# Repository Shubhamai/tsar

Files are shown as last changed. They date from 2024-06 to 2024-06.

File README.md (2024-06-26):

# Tsar

This repository contains Tsar flight computer that I have been developing for autonomous vehicles. The goal is to build a general-purpose & fully programmable flight computer that can be used for any autonomous model vehicles. The design is intended to be modular, cost-effective, and easy to manufacture.

The PCB is designed in KiCad and updated to version 8.0.3.

## Version History

### V3 [Latest Version]

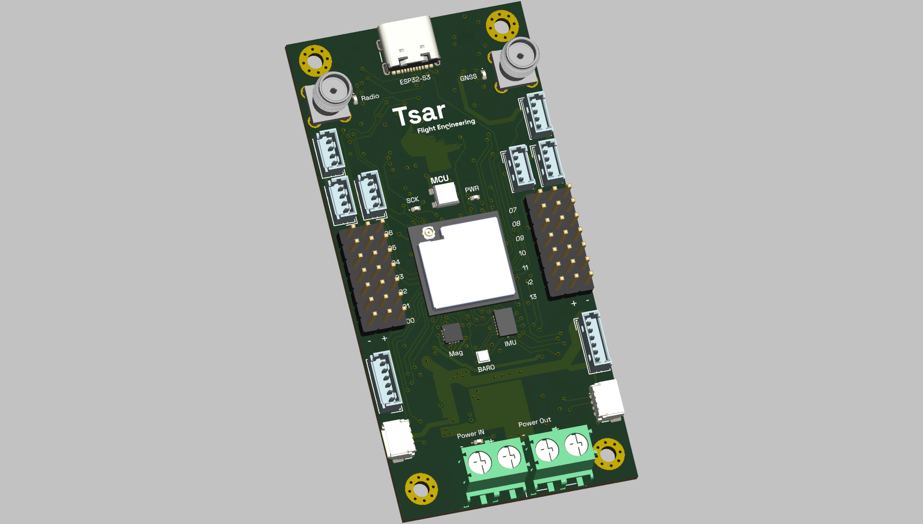
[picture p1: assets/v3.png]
V3


The design is very similar to V2 but with different IO style and no pyro channels. The secondary chip is STM32G0 for a lower number of components. The design is still in progress.

#### Key Features:
- Main Dual core ESP32-S3
- Secondary STM32G0 as an IO extender
- 2.4GHz SX1280 radio
- Ublox-M10S GNSS
- BMI088 IMU (up to ± 24 g, ± 2000°/s)
- BMP390 barometer (up to 10KM), MMC5983MA magnetometer for heading
- SD card and flash (ESP32-S3 inbuilt) for data logging & storage
- 14 PWM channels (combined 3A)
- ~20 auxiliary outputs with SPI, I2C, analog, digital pins, etc.
- 6-16V power input, (reverse+over+under)-voltage, over-current protection
- Dimensions: 40mm width, 82mm height

### V2 [April 2024]

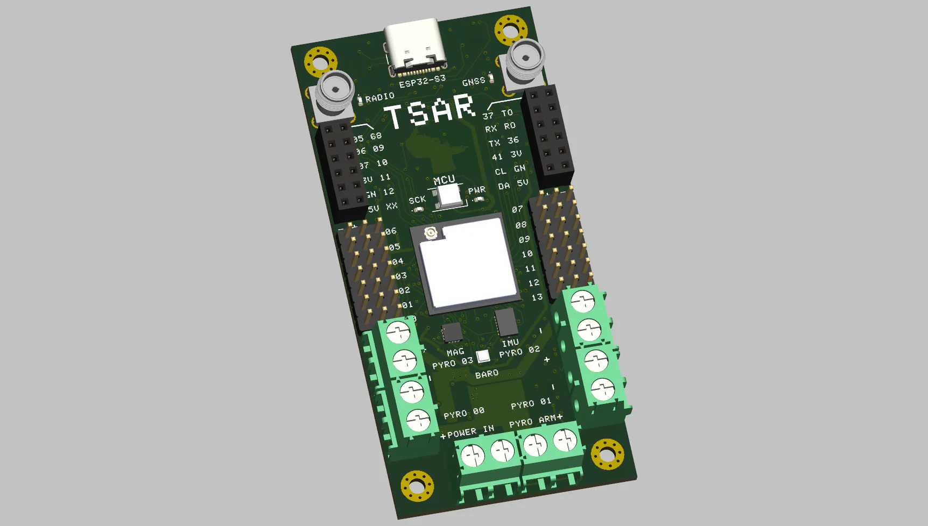
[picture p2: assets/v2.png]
V2


With learnings from V1, V2 was designed to be more cost-effective, less complex, and easier to manufacture. The BOM cost was around $60-80, and the board had 4 layers. With a trace width and minimum clearance of 0.2mm, QFN chips, and 0603 components, it was easier to manufacture and assemble. The board was manufactured and partially tested but not yet used in flight.

#### Key Features:
- Main Dual core ESP32-S3
- Secondary RP2040 as an IO extender
- 2.4GHz SX1280 radio
- Ublox-M10S GNSS
- BMI088 IMU (up to ± 24 g, ± 2000°/s)
- BMP390 barometer (up to 10KM), MMC5983MA magnetometer for heading
- 4 pyro channels (up to 16V, 4A) with continuity
- SD card and flash (ESP32-S3 inbuilt) for data logging & storage
- 14 PWM channels (combined 3A)
- 17 auxiliary outputs with SPI, I2C, analog, digital pins, etc.
- 6-16V power input, (reverse+over+under)-voltage, over-current protection
- Dimensions: 40mm width, 82mm height

### V1 [March 2024]

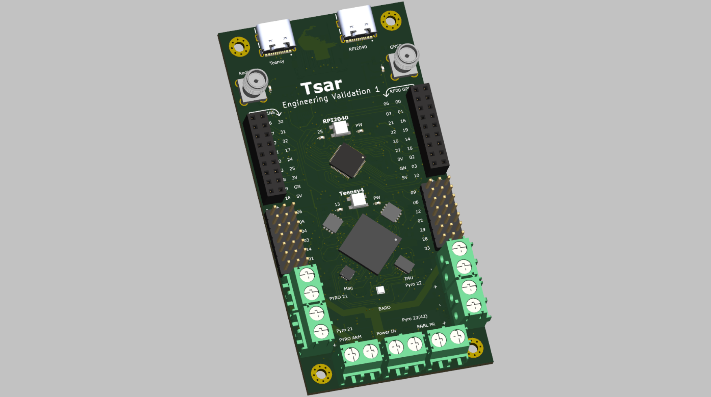
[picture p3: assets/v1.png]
V1


The first attempt at designing a flight computer. The design was powerful, using Teensy, but highly complex and less cost-effective. The BOM cost was around $120-150, and the board had 4 layers. With a trace width and minimum clearance of 0.127mm, BGA chips, and 0402 components, it was challenging to manufacture and assemble. This version was never manufactured or tested.

#### Key Features:
- Main Chip: NXP IMXRT106DVJ6B (Teensy 4.1)
- RP2040 as an IO extender
- 2.4GHz SX1280 radio
- Ublox-M10S GNSS
- BMI088 IMU (up to ± 24 g, ± 2000°/s)
- BMP390 barometer (up to 10KM), MMC5983MA magnetometer for heading
- 4 pyro channels (up to 16V, 4A) with continuity
- SD card and flash for data logging & storage
- 14 PWM channels (combined 3A)
- 30 auxiliary outputs with SPI, I2C, analog, digital pins, etc.
- 6-16V power input, (reverse+over+under)-voltage, over-current protection
- Dimensions: 50mm width, 100mm height

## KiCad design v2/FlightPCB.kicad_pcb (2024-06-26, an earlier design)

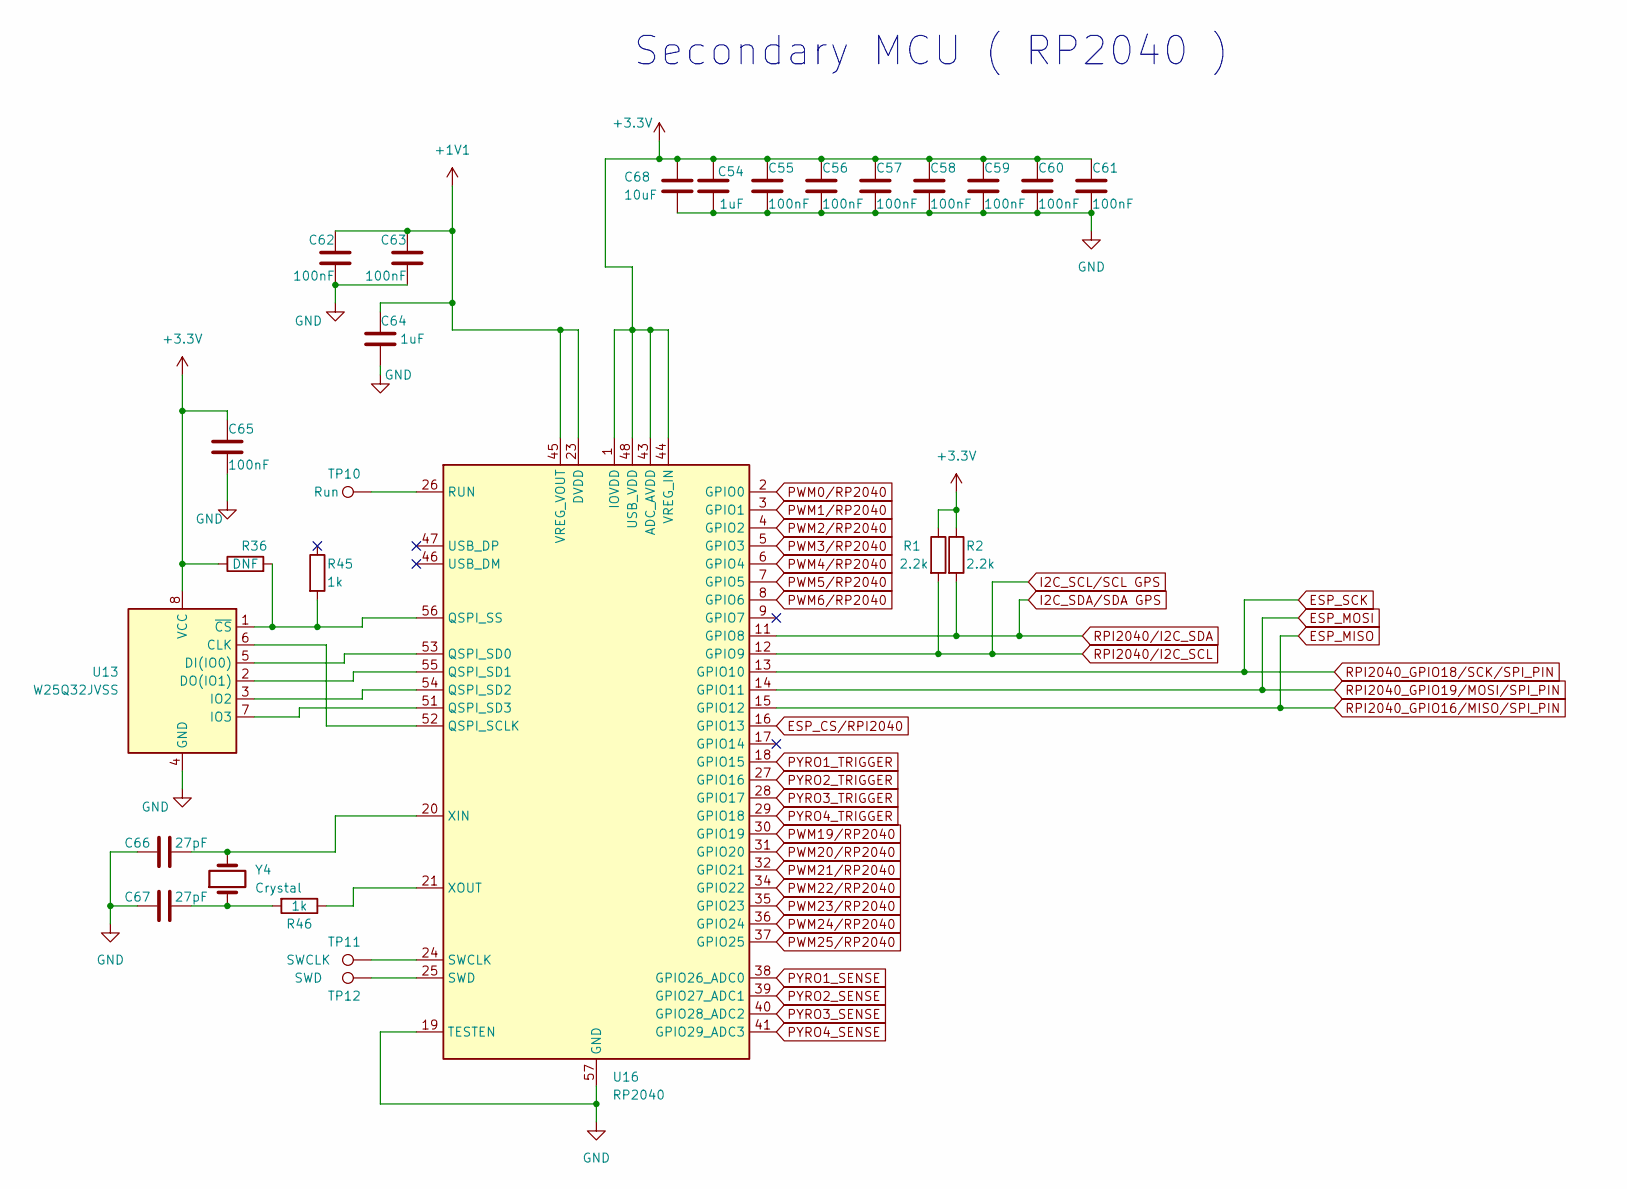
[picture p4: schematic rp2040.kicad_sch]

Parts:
C54, C64: 1uF; C_0603_1608Metric
C55, C56, C57, C58, C59, C60, C61, C62, C63, C65: 100nF; C_0603_1608Metric
C66, C67: 27pF; C_0603_1608Metric
C68: 10uF; C_0603_1608Metric
R1, R2: 2.2k; R_0603_1608Metric
R36: DNF; R_0402_1005Metric
R45, R46: 1k; R_0402_1005Metric
TP10: Run; TestPoint_Pad_D1.0mm
TP11: SWCLK; TestPoint_Pad_D2.0mm
TP12: SWD; TestPoint_Pad_D2.0mm
U13: W25Q32JVSS; SOIC-8_5.23x5.23mm_P1.27mm
U16: RP2040; QFN-56-1EP_7x7mm_P0.4mm_EP4x4mm
Y4: Crystal; Crystal_SMD_Abracon_ABM8G-4Pin_3.2x2.5mm

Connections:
+1V1: C62.1, C63.1, C64.1, U16.23 (DVDD), U16.45 (VREG_VOUT), U16.50 (DVDD)
+3.3V: C54.1, C55.1, C56.1, C57.1, C58.1, C59.1, C60.1, C61.1, C65.1, C68.1, R1.1, R2.1, R36.1, U13.8 (VCC), U16.1 (IOVDD), U16.10 (IOVDD), U16.22 (IOVDD), U16.33 (IOVDD), U16.42 (IOVDD), U16.43 (ADC_AVDD), U16.44 (VREG_IN), U16.48 (USB_VDD), U16.49 (IOVDD); also elsewhere on the board
BARO_MISO: U16.15 (GPIO12); also elsewhere on the board
BARO_MOSI: U16.14 (GPIO11); also elsewhere on the board
BARO_SCK: U16.13 (GPIO10); also elsewhere on the board
ESP_CS/RPI2040: U16.16 (GPIO13); also elsewhere on the board
ESP_SCL: R1.2, U16.12 (GPIO9); also elsewhere on the board
ESP_SDA: R2.2, U16.11 (GPIO8); also elsewhere on the board
GND: C54.2, C55.2, C56.2, C57.2, C58.2, C59.2, C60.2, C61.2, C62.2, C63.2, C64.2, C65.2, C66.1, C67.2, C68.2, U13.4 (GND), U16.19 (TESTEN), U16.57 (GND); also elsewhere on the board
unnamed: C67.1, R46.2, Y4.1
unnamed: U13.6 (CLK), U16.52 (QSPI_SCLK)
unnamed: U13.5 (DI(IO0)), U16.53 (QSPI_SD0)
unnamed: U13.2 (DO(IO1)), U16.55 (QSPI_SD1)
unnamed: U13.3 (IO2), U16.54 (QSPI_SD2)
unnamed: U13.7 (IO3), U16.51 (QSPI_SD3)
unnamed: R36.2, R45.2, U13.1 (~CS), U16.56 (QSPI_SS)
unnamed: TP10.1, U16.26 (RUN)
unnamed: TP11.1, U16.24 (SWCLK)
unnamed: TP12.1, U16.25 (SWD)
unnamed: C66.2, U16.20 (XIN), Y4.2
unnamed: R46.1, U16.21 (XOUT)
PWM0/RP2040: U16.2 (GPIO0); also elsewhere on the board
PWM1/RP2040: U16.3 (GPIO1); also elsewhere on the board
PWM2/RP2040: U16.4 (GPIO2); also elsewhere on the board
PWM3/RP2040: U16.5 (GPIO3); also elsewhere on the board
PWM4/RP2040: U16.6 (GPIO4); also elsewhere on the board
PWM5/RP2040: U16.7 (GPIO5); also elsewhere on the board
PWM6/RP2040: U16.8 (GPIO6); also elsewhere on the board
PWM19/RP2040: U16.30 (GPIO19); also elsewhere on the board
PWM20/RP2040: U16.31 (GPIO20); also elsewhere on the board
PWM21/RP2040: U16.32 (GPIO21); also elsewhere on the board
PWM22/RP2040: U16.34 (GPIO22); also elsewhere on the board
PWM23/RP2040: U16.35 (GPIO23); also elsewhere on the board
PWM24/RP2040: U16.36 (GPIO24); also elsewhere on the board
PWM25/RP2040: U16.37 (GPIO25); also elsewhere on the board
PYRO1_SENSE: U16.38 (GPIO26_ADC0); also elsewhere on the board
PYRO1_TRIGGER: U16.18 (GPIO15); also elsewhere on the board
PYRO2_SENSE: U16.39 (GPIO27_ADC1); also elsewhere on the board
PYRO2_TRIGGER: U16.27 (GPIO16); also elsewhere on the board
PYRO3_SENSE: U16.40 (GPIO28_ADC2); also elsewhere on the board
PYRO3_TRIGGER: U16.28 (GPIO17); also elsewhere on the board
PYRO4_SENSE: U16.41 (GPIO29_ADC3); also elsewhere on the board
PYRO4_TRIGGER: U16.29 (GPIO18); also elsewhere on the board

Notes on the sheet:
Secondary MCU ( RP2040 )

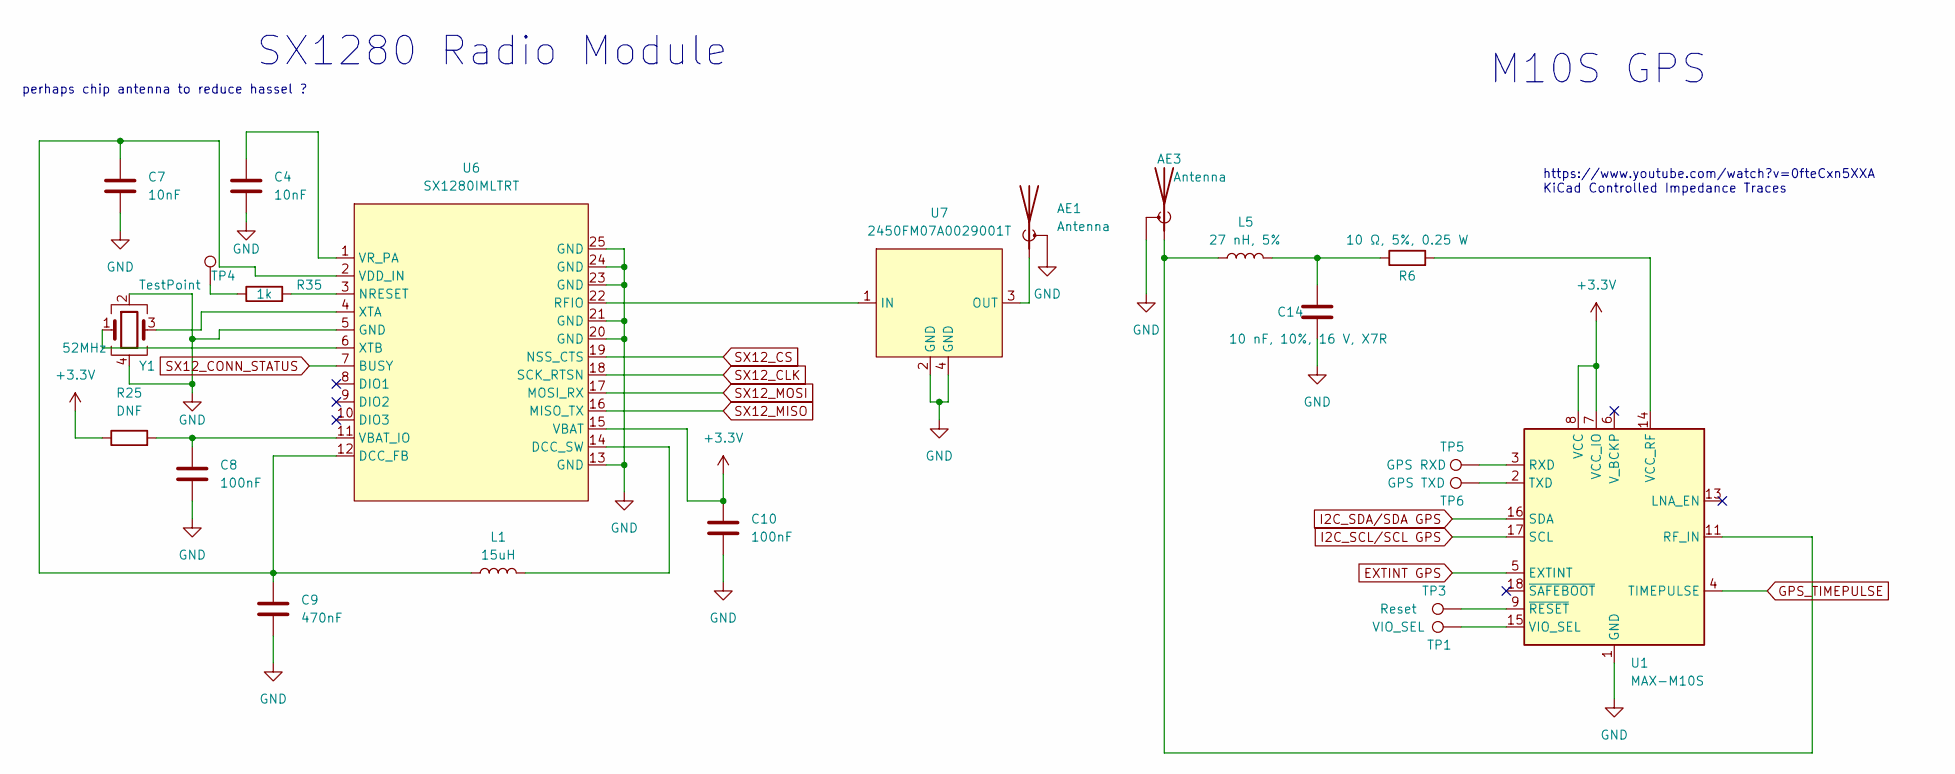
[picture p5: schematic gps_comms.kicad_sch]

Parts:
AE1, AE3: Antenna; SMA_Amphenol_901-144_Vertical
C4, C7: 10nF; C_0603_1608Metric
C8, C10: 100nF; C_0603_1608Metric
C9: 470nF; C_0402_1005Metric
C14: 10 nF, 10%, 16 V, X7R; C_0603_1608Metric
L1: 15uH; L_0805_2012Metric
L5: 27 nH, 5%; L_0402_1005Metric
R6: 10 Ω, 5%, 0.25 W; R_0402_1005Metric
R25: DNF; R_0402_1005Metric
R35: 1k; R_0402_1005Metric
TP1: VIO_SEL; TestPoint_Pad_D1.0mm
TP3: Reset; TestPoint_Pad_D1.0mm
TP4: TestPoint; TestPoint_Pad_D1.0mm
TP5: GPS RXD; TestPoint_Pad_D1.0mm
TP6: GPS TXD; TestPoint_Pad_D1.0mm
U1: MAX-M10S; ublox_MAX
U6: SX1280IMLTRT; QFN-24-1EP_4x4mm_P0.5mm_EP2.7x2.7mm
U7: 2450FM07A0029001T
Y1: 52MHz; Crystal_SMD_2016-4Pin_2.0x1.6mm

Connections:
+3.3V: C10.1, R25.1, U1.7 (VCC_IO), U1.8 (VCC), U6.15 (VBAT); also elsewhere on the board
BARO_MISO: U6.16 (MISO_TX); also elsewhere on the board
BARO_MOSI: U6.17 (MOSI_RX); also elsewhere on the board
BARO_SCK: U6.18 (SCK_RTSN); also elsewhere on the board
ESP_SCL: U1.17 (SCL); also elsewhere on the board
ESP_SDA: U1.16 (SDA); also elsewhere on the board
EXTINT GPS: U1.5 (EXTINT); also elsewhere on the board
GND: AE1.2 (Shield), AE3.2 (Shield), C4.2, C7.2, C8.2, C9.2, C10.2, C14.1, U1.1 (GND), U1.10 (GND), U1.12 (GND), U6.5 (GND), U6.13 (GND), U6.20 (GND), U6.21 (GND), U6.23 (GND), U6.24 (GND), U6.25 (GND), U7.2 (GND), U7.4 (GND), Y1.2, Y1.4; also elsewhere on the board
GPS_TIMEPULSE: U1.4 (TIMEPULSE); also elsewhere on the board
unnamed: AE1.1 (A), U7.3 (OUT)
unnamed: AE3.1 (A), L5.1, U1.11 (RF_IN)
unnamed: C14.2, L5.2, R6.1
unnamed: R35.1, TP4.1
unnamed: TP5.1, U1.3 (RXD)
unnamed: TP6.1, U1.2 (TXD)
unnamed: R6.2, U1.14 (VCC_RF)
unnamed: TP1.1, U1.15 (VIO_SEL)
unnamed: TP3.1, U1.9 (~RESET)
unnamed: C7.1, C9.1, L1.1, U6.2 (VDD_IN), U6.12 (DCC_FB)
unnamed: L1.2, U6.14 (DCC_SW)
unnamed: R35.2, U6.3 (NRESET)
unnamed: U6.22 (RFIO), U7.1 (IN)
unnamed: C8.1, R25.2, U6.11 (VBAT_IO)
unnamed: C4.1, U6.1 (VR_PA)
unnamed: U6.4 (XTA), Y1.3
unnamed: U6.6 (XTB), Y1.1
SX12_CONN_STATUS: U6.7 (BUSY); also elsewhere on the board
SX12_CS: U6.19 (NSS_CTS); also elsewhere on the board

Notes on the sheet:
perhaps chip antenna to reduce hassel ?
https://www.youtube.com/watch?v=0fteCxn5XXA KiCad Controlled Impedance Traces
M10S GPS
SX1280 Radio Module

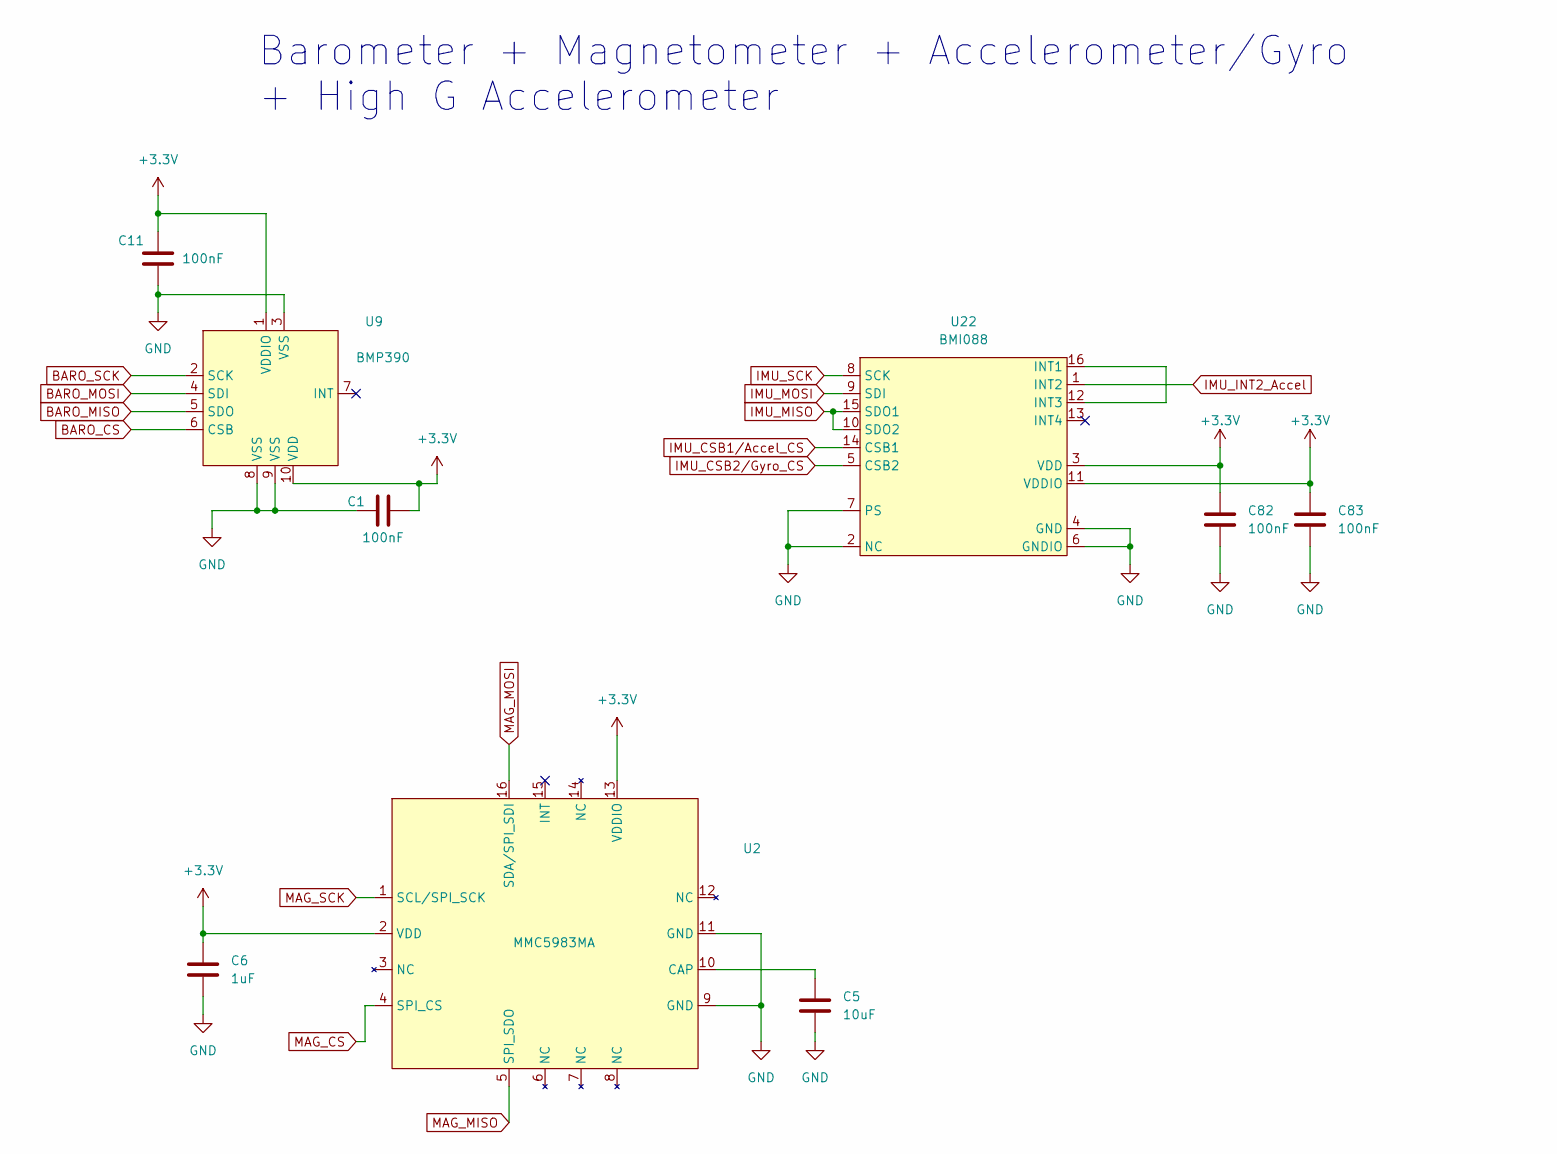
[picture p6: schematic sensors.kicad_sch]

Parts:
C1, C11, C82, C83: 100nF; C_0603_1608Metric
C5: 10uF; C_0603_1608Metric
C6: 1uF; C_0603_1608Metric
U2: MMC5983MA
U9: BMP390
U22: BMI088

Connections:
+3.3V: C1.2, C6.1, C11.2, C82.1, C83.1, U2.2 (VDD), U2.13 (VDDIO), U9.1 (VDDIO), U9.10 (VDD), U22.3 (VDD), U22.11 (VDDIO); also elsewhere on the board
BARO_CS: U9.6 (CSB); also elsewhere on the board
BARO_MISO: U2.5 (SPI_SDO), U9.5 (SDO), U22.10 (SDO2), U22.15 (SDO1); also elsewhere on the board
BARO_MOSI: U2.16 (SDA/SPI_SDI), U9.4 (SDI), U22.9 (SDI); also elsewhere on the board
BARO_SCK: U2.1 (SCL/SPI_SCK), U9.2 (SCK), U22.8 (SCK); also elsewhere on the board
GND: C1.1, C5.2, C6.2, C11.1, C82.2, C83.2, U2.9 (GND), U2.11 (GND), U9.3 (VSS), U9.8 (VSS), U9.9 (VSS), U22.2 (NC), U22.4 (GND), U22.6 (GNDIO), U22.7 (PS); also elsewhere on the board
IMU_CSB1/Accel_CS: U22.14 (CSB1); also elsewhere on the board
IMU_CSB2/Gyro_CS: U22.5 (CSB2); also elsewhere on the board
IMU_INT2_Accel: U22.1 (INT2); also elsewhere on the board
MAG_CS: U2.4 (SPI_CS); also elsewhere on the board
unnamed: C5.1, U2.10 (CAP)
unnamed: U22.12 (INT3), U22.16 (INT1)

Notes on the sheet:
Barometer + Magnetometer + Accelerometer/Gyro + High G Accelerometer

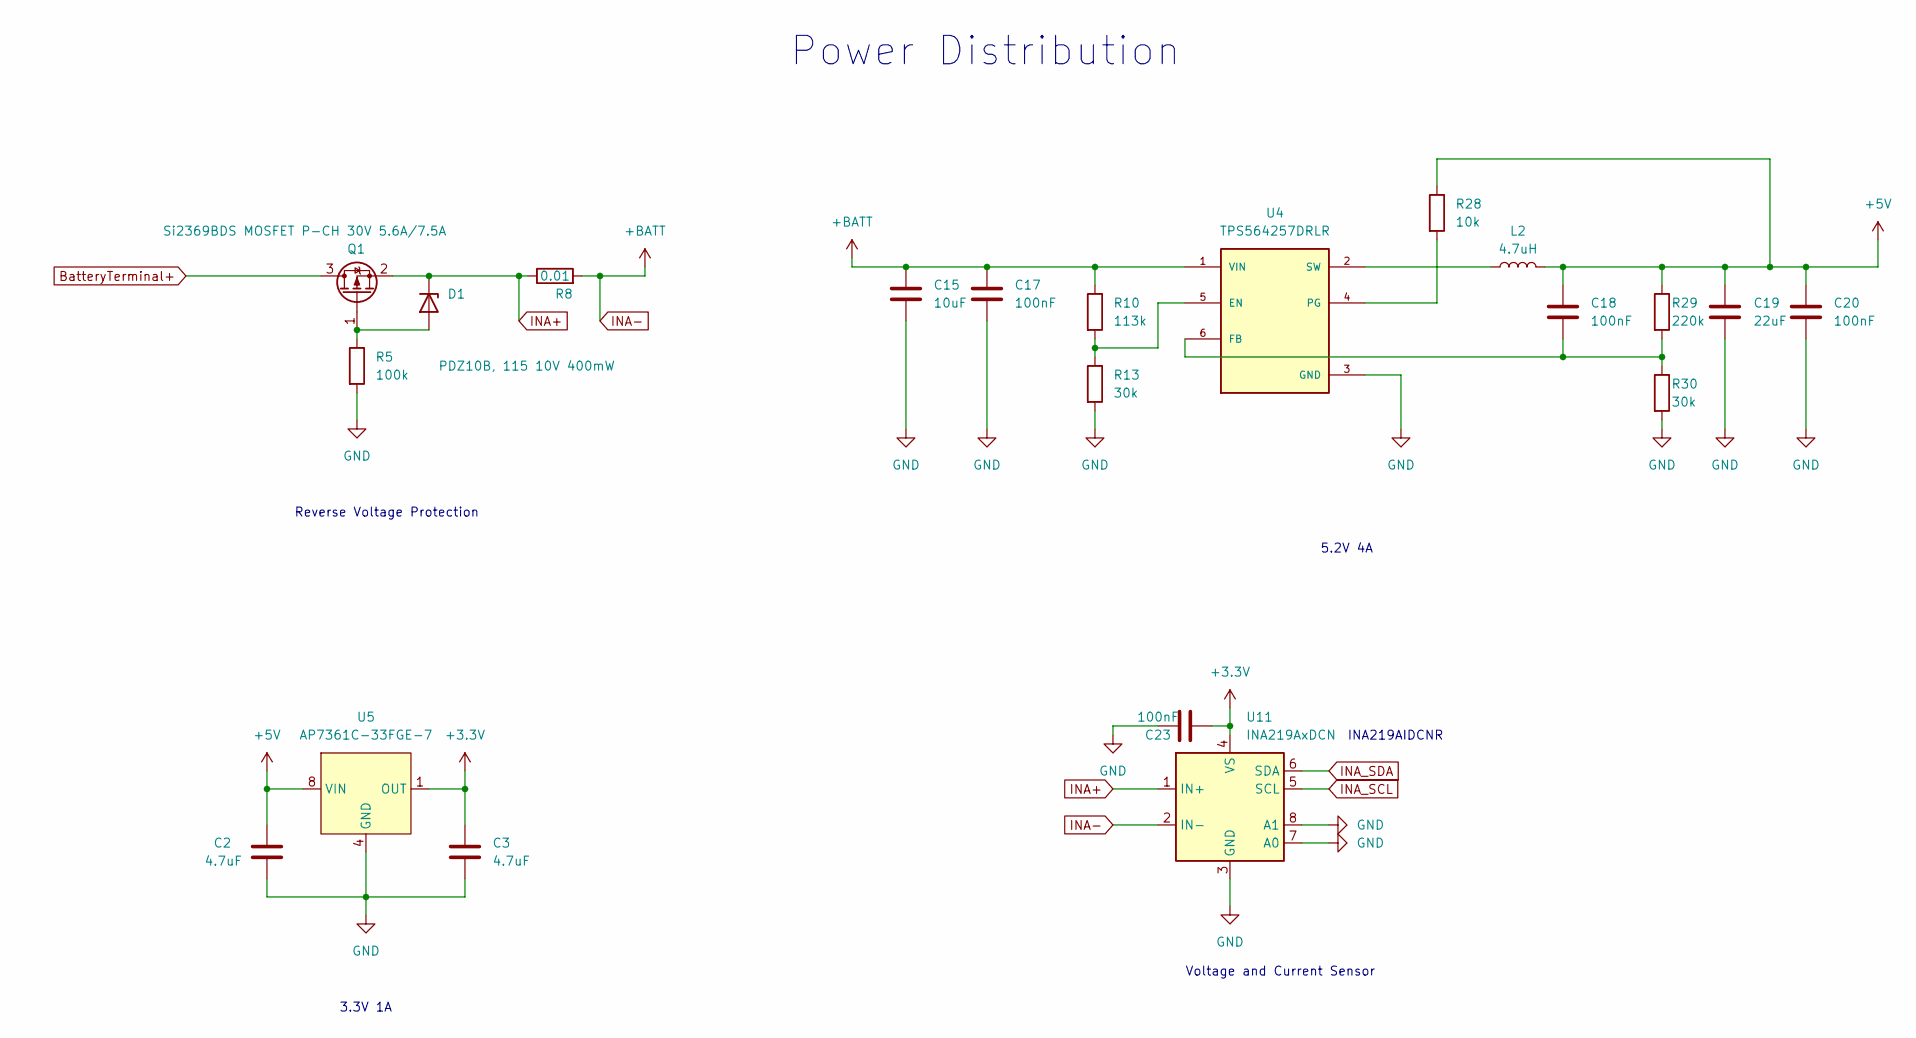
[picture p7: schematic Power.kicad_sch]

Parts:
C2, C3: 4.7uF; C_0603_1608Metric
C15: 10uF; C_0603_1608Metric
C17, C18, C20, C23: 100nF; C_0603_1608Metric
C19: 22uF; C_0805_2012Metric
D1: PDZ10B, 115 10V 400mW; D_0805_2012Metric
L2: 4.7uH; L_Cenker_CKCS8040
Q1: Si2369BDS MOSFET P-CH 30V 5.6A/7.5A; SOT-23
R5: 100k; R_0805_2012Metric
R8: 0.01; R_2512_6332Metric
R10: 113k; R_0603_1608Metric
R13, R30: 30k; R_0603_1608Metric
R28: 10k; R_0603_1608Metric
R29: 220k; R_0603_1608Metric
U4: TPS564257DRLR; SOT50P160X60-6N; PARTREV A
U5: AP7361C-33FGE-7; MLF-8-1EP_3x3mm_P0.65mm_EP1.55x2.3mm
U11: INA219AxDCN; SOT-23-8

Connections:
+3.3V: C3.1, C23.2, U5.1 (OUT), U11.4 (VS); also elsewhere on the board
BatteryTerminal+: Q1.3 (D); also elsewhere on the board
ESP_SCL: U11.5 (SCL); also elsewhere on the board
ESP_SDA: U11.6 (SDA); also elsewhere on the board
GND: C2.2, C3.2, C15.2, C17.2, C19.2, C20.2, C23.1, R5.2, R13.2, R30.2, U4.3 (GND), U5.4 (GND), U11.3 (GND), U11.7 (A0), U11.8 (A1); also elsewhere on the board
INA+: D1.1 (K), Q1.2 (S), R8.1, U11.1 (IN+)
INA-: C15.1, C17.1, R8.2, R10.1, U4.1 (VIN), U11.2 (IN-); also elsewhere on the board
unnamed: D1.2 (A), Q1.1 (G), R5.1
unnamed: R10.2, R13.1, U4.5 (EN)
unnamed: C18.2, R29.2, R30.1, U4.6 (FB)
unnamed: R28.2, U4.4 (PG)
unnamed: L2.1, U4.2 (SW)

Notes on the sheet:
INA219AIDCNR
Voltage and Current Sensor
3.3V 1A
Reverse Voltage Protection
5.2V 4A
Power Distribution

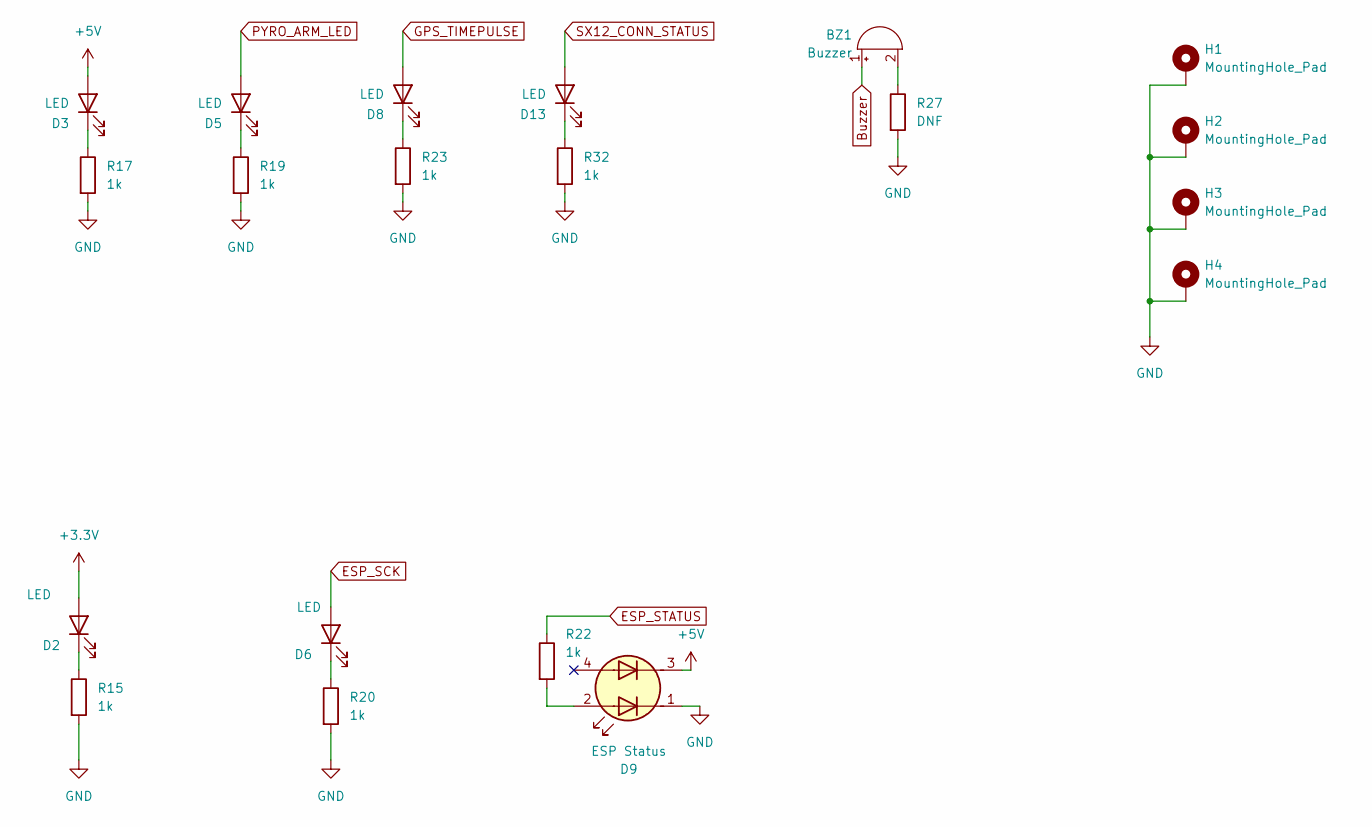
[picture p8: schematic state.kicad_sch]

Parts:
BZ1: Buzzer; Buzzer_CUI_CPT-9019S-SMT
D2, D3, D5, D6, D8, D13: LED; LED_0402_1005Metric
D9: ESP Status; IN-PI22TAT5R5G5B
H1, H2, H3, H4: MountingHole_Pad; MountingHole_2.7mm_M2.5_Pad_Via
R15, R17, R19, R20, R22, R23, R32: 1k; R_0402_1005Metric
R27: DNF; R_0402_1005Metric

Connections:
+3.3V: D2.2 (A); also elsewhere on the board
BARO_SCK: D6.2 (A); also elsewhere on the board
Buzzer: BZ1.1 (+); also elsewhere on the board
ESP_STATUS: R22.1; also elsewhere on the board
GND: D9.1 (A1), H1.1, H2.1, H3.1, H4.1, R15.2, R17.2, R19.2, R20.2, R23.2, R27.2, R32.2; also elsewhere on the board
GPS_TIMEPULSE: D8.2 (A); also elsewhere on the board
unnamed: BZ1.2 (-), R27.1
unnamed: D2.1 (K), R15.1
unnamed: D3.1 (K), R17.1
unnamed: D5.1 (K), R19.1
unnamed: D6.1 (K), R20.1
unnamed: D8.1 (K), R23.1
unnamed: D9.2 (K1), R22.2
unnamed: D13.1 (K), R32.1
PYRO_ARM_LED: D5.2 (A); also elsewhere on the board
SX12_CONN_STATUS: D13.2 (A); also elsewhere on the board

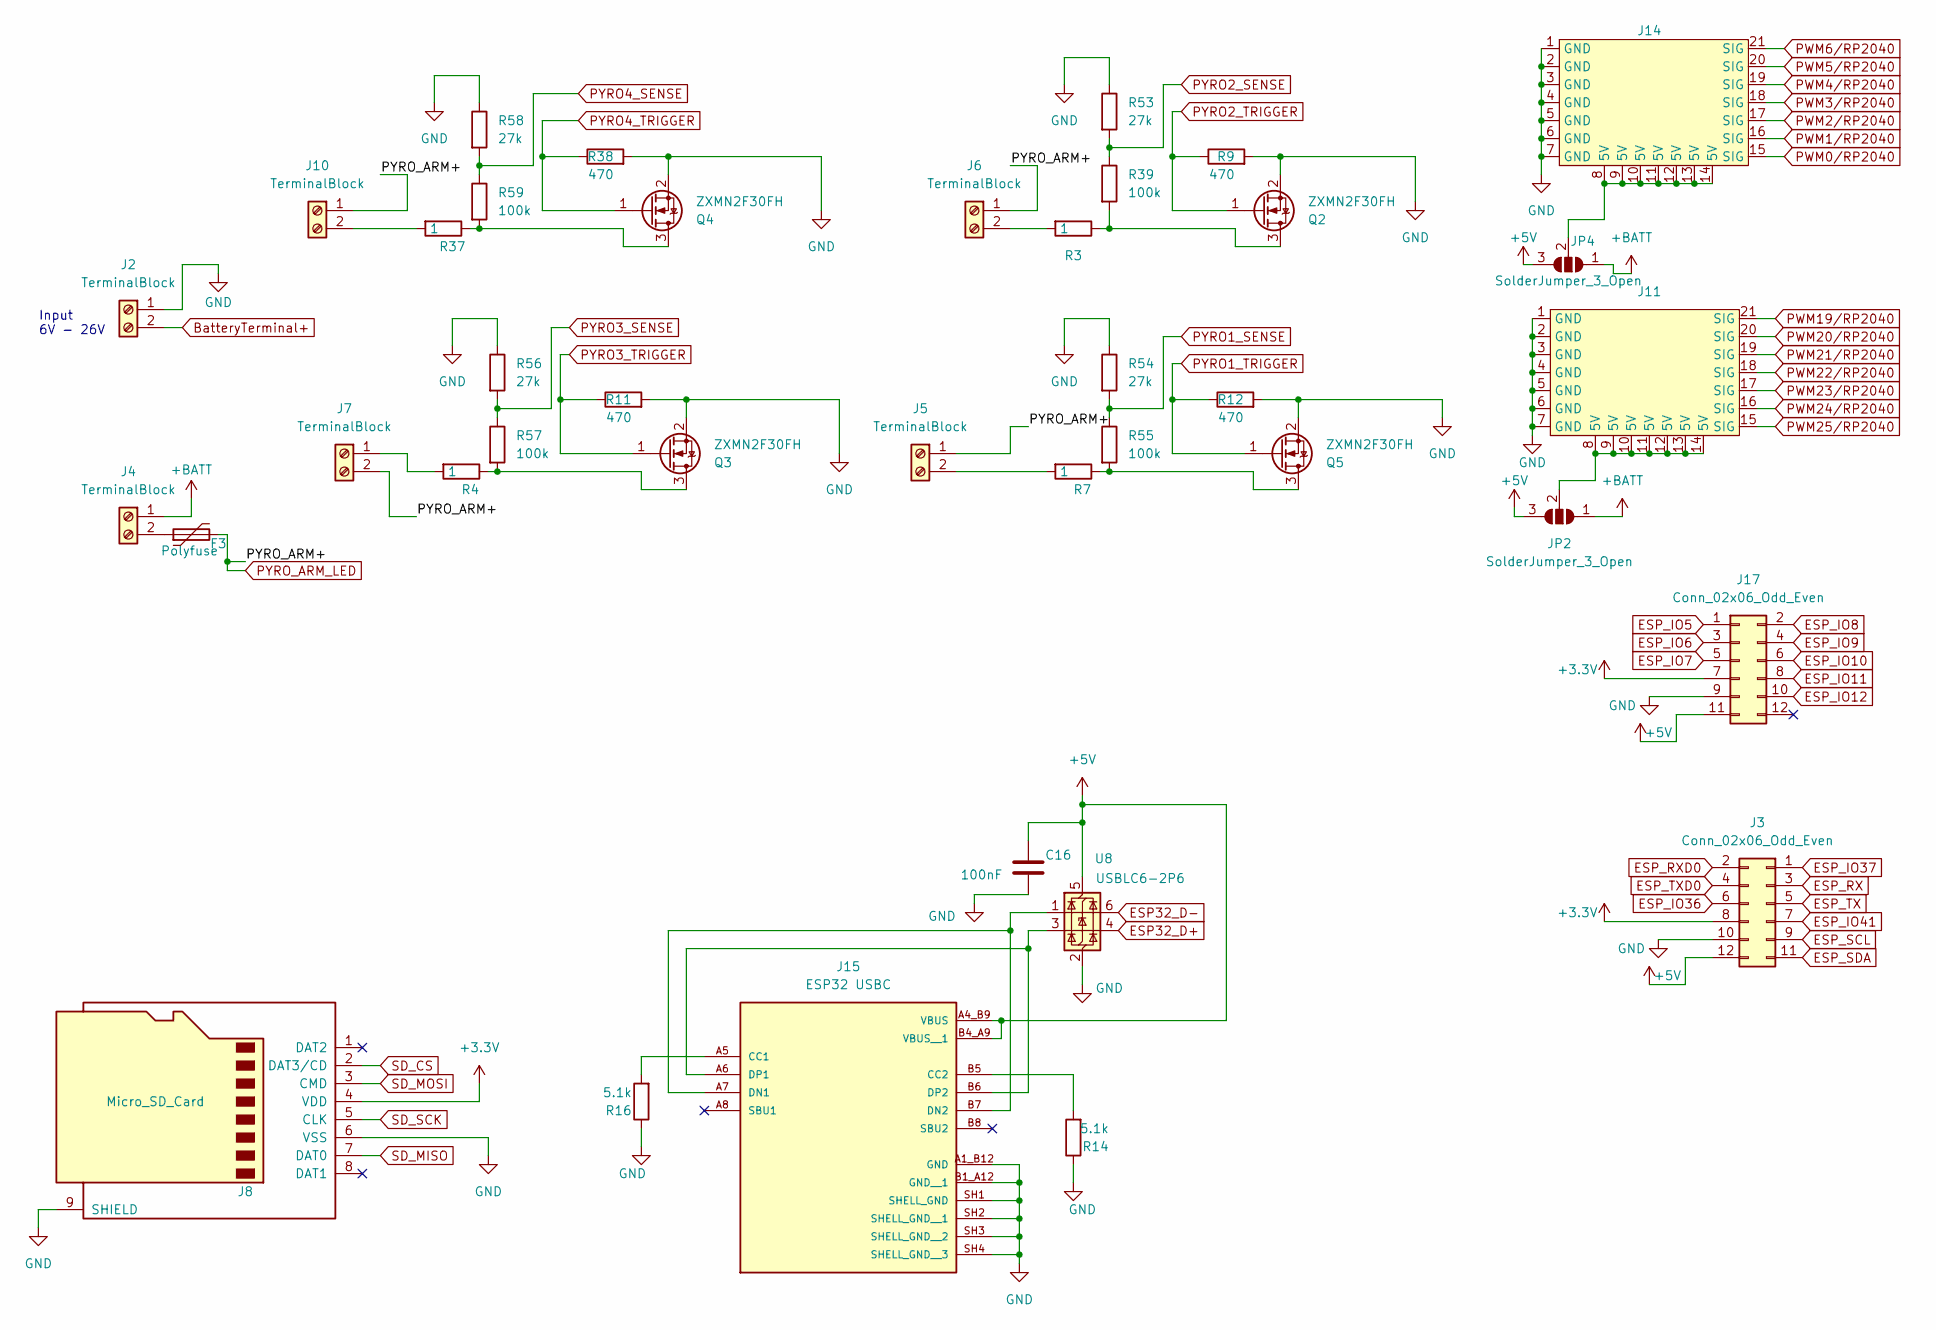
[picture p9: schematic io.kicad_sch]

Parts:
C16: 100nF; C_0603_1608Metric
F3: Polyfuse; Fuse_1812_4532Metric
J2, J4, J5, J6, J7, J10: TerminalBlock; TerminalBlock_Phoenix_PT-1,5-2-5.0-H_1x02_P5.00mm_Horizontal
J3, J17: Conn_02x06_Odd_Even; PinSocket_2x06_P2.54mm_Vertical
J8: Micro_SD_Card; microSD_HC_Molex_47219-2001
J11: PinHeader_3x05_P2.54mm_Vertical_Left
J14: PinHeader_3x05_P2.54mm_Vertical_Right
J15: ESP32 USBC; GCT_USB4105-GF-A; PARTREV B3
JP2, JP4: SolderJumper_3_Open; SolderJumper-3_P2.0mm_Open_TrianglePad1.0x1.5mm
Q2, Q3, Q4, Q5: ZXMN2F30FH; SOT-23
R3, R4, R7, R37: 1; R_0603_1608Metric
R9, R11, R12, R38: 470; R_0603_1608Metric
R14, R16: 5.1k; R_0603_1608Metric
R39, R55, R57, R59: 100k; R_0805_2012Metric
R53, R54, R56, R58: 27k; R_0603_1608Metric
U8: USBLC6-2P6; SOT-666

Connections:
+3.3V: J3.8, J8.4 (VDD), J17.7; also elsewhere on the board
BARO_MISO: J8.7 (DAT0); also elsewhere on the board
BARO_MOSI: J8.3 (CMD); also elsewhere on the board
BARO_SCK: J8.5 (CLK); also elsewhere on the board
BatteryTerminal+: J2.2; also elsewhere on the board
ESP32_D+: U8.4 (I/O2); also elsewhere on the board
ESP32_D-: U8.6 (I/O1); also elsewhere on the board
ESP_IO5: J17.1; also elsewhere on the board
ESP_IO6: J17.3; also elsewhere on the board
ESP_IO7: J17.5; also elsewhere on the board
ESP_IO8: J17.2; also elsewhere on the board
ESP_IO9: J17.4; also elsewhere on the board
ESP_IO10: J17.6; also elsewhere on the board
ESP_IO11: J17.8; also elsewhere on the board
ESP_IO12: J17.10; also elsewhere on the board
ESP_IO36: J3.6; also elsewhere on the board
ESP_IO37: J3.1; also elsewhere on the board
ESP_IO41: J3.7; also elsewhere on the board
ESP_RX: J3.3; also elsewhere on the board
ESP_RXD0: J3.2; also elsewhere on the board
ESP_SCL: J3.9; also elsewhere on the board
ESP_SDA: J3.11; also elsewhere on the board
ESP_TX: J3.5; also elsewhere on the board
ESP_TXD0: J3.4; also elsewhere on the board
GND: C16.2, J2.1, J3.10, J8.6 (VSS), J8.9 (SHIELD), J11.1 (GND), J11.2 (GND), J11.3 (GND), J11.4 (GND), J11.5 (GND), J11.6 (GND), J11.7 (GND), J14.1 (GND), J14.2 (GND), J14.3 (GND), J14.4 (GND), J14.5 (GND), J14.6 (GND), J14.7 (GND), J15.A1_B12 (GND), J15.B1_A12 (GND__1), J15.SH1 (SHELL_GND), J15.SH2 (SHELL_GND__1), J15.SH3 (SHELL_GND__2), J15.SH4 (SHELL_GND__3), J17.9, Q2.2 (S), Q3.2 (S), Q4.2 (S), Q5.2 (S), R9.2, R11.2, R12.2, R14.1, R16.1, R38.2, R53.1, R54.1, R56.1, R58.1, U8.2 (GND); also elsewhere on the board
INA-: J4.1, JP2.1 (A), JP4.1 (A); also elsewhere on the board
unnamed: F3.1, J4.2
unnamed: J5.2, R7.2
unnamed: J6.2, R3.2
unnamed: J7.1, R4.2
unnamed: J10.2, R37.2
unnamed: J15.A5 (CC1), R16.2
unnamed: J15.B5 (CC2), R14.2
unnamed: J15.A7 (DN1), J15.B7 (DN2), U8.1 (I/O1)
unnamed: J15.A6 (DP1), J15.B6 (DP2), U8.3 (I/O2)
unnamed: Q2.3 (D), R3.1, R39.2
unnamed: Q3.3 (D), R4.1, R57.2
unnamed: Q4.3 (D), R37.1, R59.2
unnamed: Q5.3 (D), R7.1, R55.2
PWM0/RP2040: J14.15 (SIG); also elsewhere on the board
PWM1/RP2040: J14.16 (SIG); also elsewhere on the board
PWM2/RP2040: J14.17 (SIG); also elsewhere on the board
PWM3/RP2040: J14.18 (SIG); also elsewhere on the board
PWM4/RP2040: J14.19 (SIG); also elsewhere on the board
PWM5/RP2040: J14.20 (SIG); also elsewhere on the board
PWM6/RP2040: J14.21 (SIG); also elsewhere on the board
PWM19/RP2040: J11.21 (SIG); also elsewhere on the board
PWM20/RP2040: J11.20 (SIG); also elsewhere on the board
PWM21/RP2040: J11.19 (SIG); also elsewhere on the board
PWM22/RP2040: J11.18 (SIG); also elsewhere on the board
PWM23/RP2040: J11.17 (SIG); also elsewhere on the board
PWM24/RP2040: J11.16 (SIG); also elsewhere on the board
PWM25/RP2040: J11.15 (SIG); also elsewhere on the board
PYRO1_SENSE: R54.2, R55.1; also elsewhere on the board
PYRO1_TRIGGER: Q5.1 (G), R12.1; also elsewhere on the board
PYRO2_SENSE: R39.1, R53.2; also elsewhere on the board
PYRO2_TRIGGER: Q2.1 (G), R9.1; also elsewhere on the board
PYRO3_SENSE: R56.2, R57.1; also elsewhere on the board
PYRO3_TRIGGER: Q3.1 (G), R11.1; also elsewhere on the board
PYRO4_SENSE: R58.2, R59.1; also elsewhere on the board
PYRO4_TRIGGER: Q4.1 (G), R38.1; also elsewhere on the board
PYRO_ARM_LED: F3.2, J5.1, J6.1, J7.2, J10.1; also elsewhere on the board
SD_CS: J8.2 (DAT3/CD); also elsewhere on the board

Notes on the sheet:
Input 6V - 26V

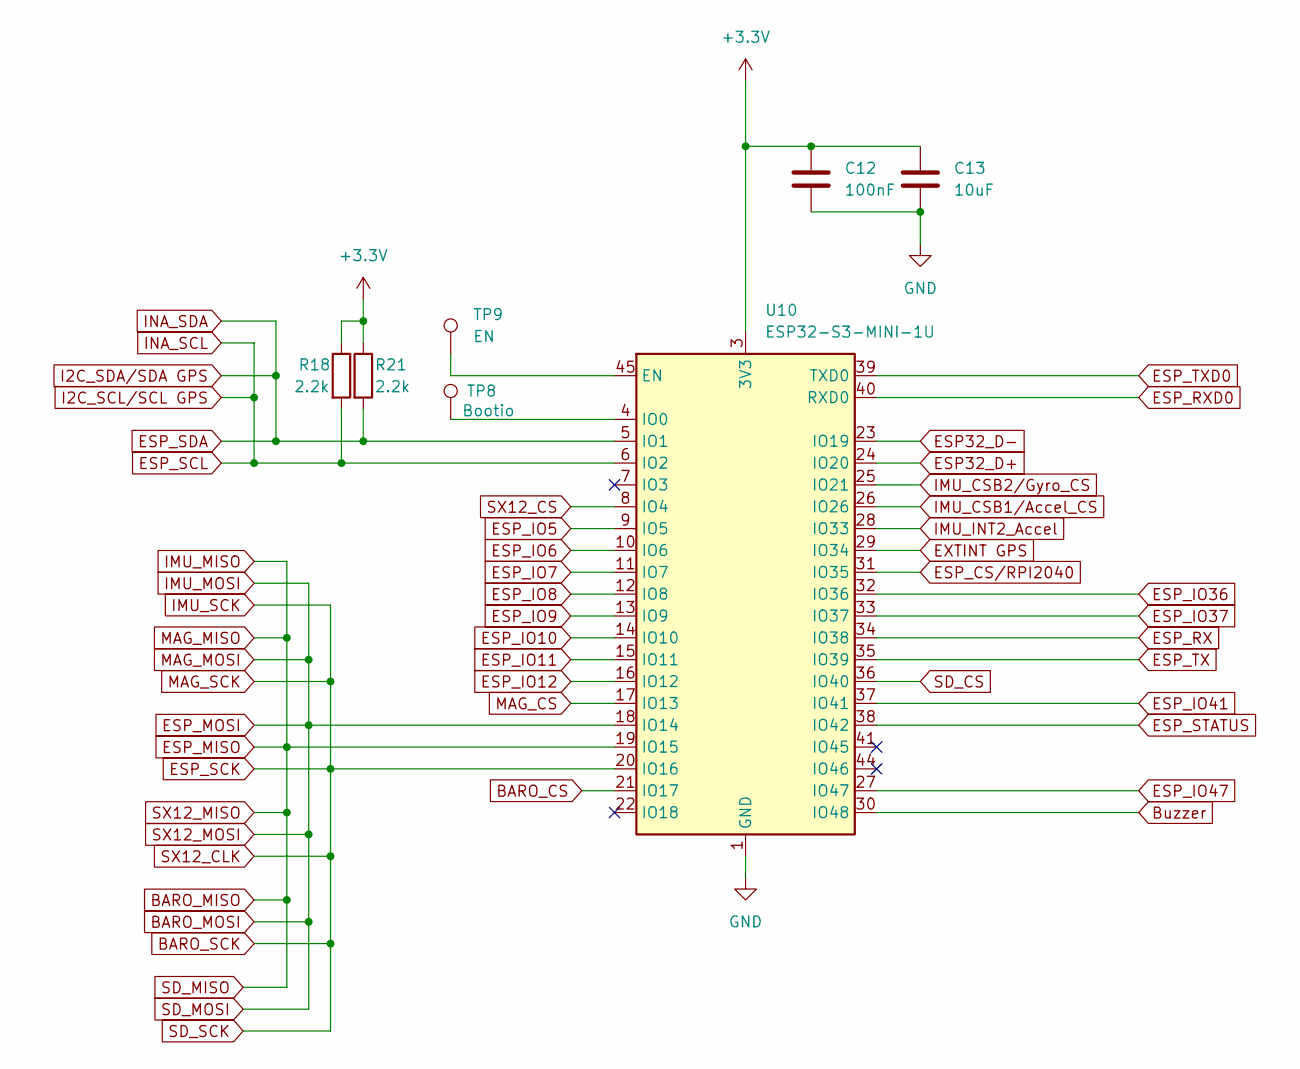
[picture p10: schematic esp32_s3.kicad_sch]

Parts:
C12: 100nF; C_0603_1608Metric
C13: 10uF; C_0603_1608Metric
R18, R21: 2.2k; R_0603_1608Metric
TP8: Bootio; TestPoint_Pad_D1.0mm
TP9: EN; TestPoint_Pad_D1.0mm
U10: ESP32-S3-MINI-1U; ESP32-S2-MINI-1U

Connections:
+3.3V: C12.1, C13.1, R18.1, R21.1, U10.3 (3V3); also elsewhere on the board
BARO_CS: U10.21 (IO17); also elsewhere on the board
BARO_MISO: U10.19 (IO15); also elsewhere on the board
BARO_MOSI: U10.18 (IO14); also elsewhere on the board
BARO_SCK: U10.20 (IO16); also elsewhere on the board
Buzzer: U10.30 (IO48); also elsewhere on the board
ESP32_D+: U10.24 (IO20); also elsewhere on the board
ESP32_D-: U10.23 (IO19); also elsewhere on the board
ESP_CS/RPI2040: U10.31 (IO35); also elsewhere on the board
ESP_IO5: U10.9 (IO5); also elsewhere on the board
ESP_IO6: U10.10 (IO6); also elsewhere on the board
ESP_IO7: U10.11 (IO7); also elsewhere on the board
ESP_IO8: U10.12 (IO8); also elsewhere on the board
ESP_IO9: U10.13 (IO9); also elsewhere on the board
ESP_IO10: U10.14 (IO10); also elsewhere on the board
ESP_IO11: U10.15 (IO11); also elsewhere on the board
ESP_IO12: U10.16 (IO12); also elsewhere on the board
ESP_IO36: U10.32 (IO36); also elsewhere on the board
ESP_IO37: U10.33 (IO37); also elsewhere on the board
ESP_IO41: U10.37 (IO41); also elsewhere on the board
ESP_IO47: U10.27 (IO47)
ESP_RX: U10.34 (IO38); also elsewhere on the board
ESP_RXD0: U10.40 (RXD0); also elsewhere on the board
ESP_SCL: R18.2, U10.6 (IO2); also elsewhere on the board
ESP_SDA: R21.2, U10.5 (IO1); also elsewhere on the board
ESP_STATUS: U10.38 (IO42); also elsewhere on the board
ESP_TX: U10.35 (IO39); also elsewhere on the board
ESP_TXD0: U10.39 (TXD0); also elsewhere on the board
EXTINT GPS: U10.29 (IO34); also elsewhere on the board
GND: C12.2, C13.2, U10.1 (GND), U10.2 (GND), U10.42 (GND), U10.43 (GND), U10.46 (GND), U10.47 (GND), U10.48 (GND), U10.49 (GND), U10.50 (GND), U10.51 (GND), U10.52 (GND), U10.53 (GND), U10.54 (GND), U10.55 (GND), U10.56 (GND), U10.57 (GND), U10.58 (GND), U10.59 (GND), U10.60 (GND), U10.61 (GND), U10.62 (GND), U10.63 (GND), U10.64 (GND), U10.65 (GND); also elsewhere on the board
IMU_CSB1/Accel_CS: U10.26 (IO26); also elsewhere on the board
IMU_CSB2/Gyro_CS: U10.25 (IO21); also elsewhere on the board
IMU_INT2_Accel: U10.28 (IO33); also elsewhere on the board
MAG_CS: U10.17 (IO13); also elsewhere on the board
unnamed: TP9.1, U10.45 (EN)
unnamed: TP8.1, U10.4 (IO0)
SD_CS: U10.36 (IO40); also elsewhere on the board
SX12_CS: U10.8 (IO4); also elsewhere on the board

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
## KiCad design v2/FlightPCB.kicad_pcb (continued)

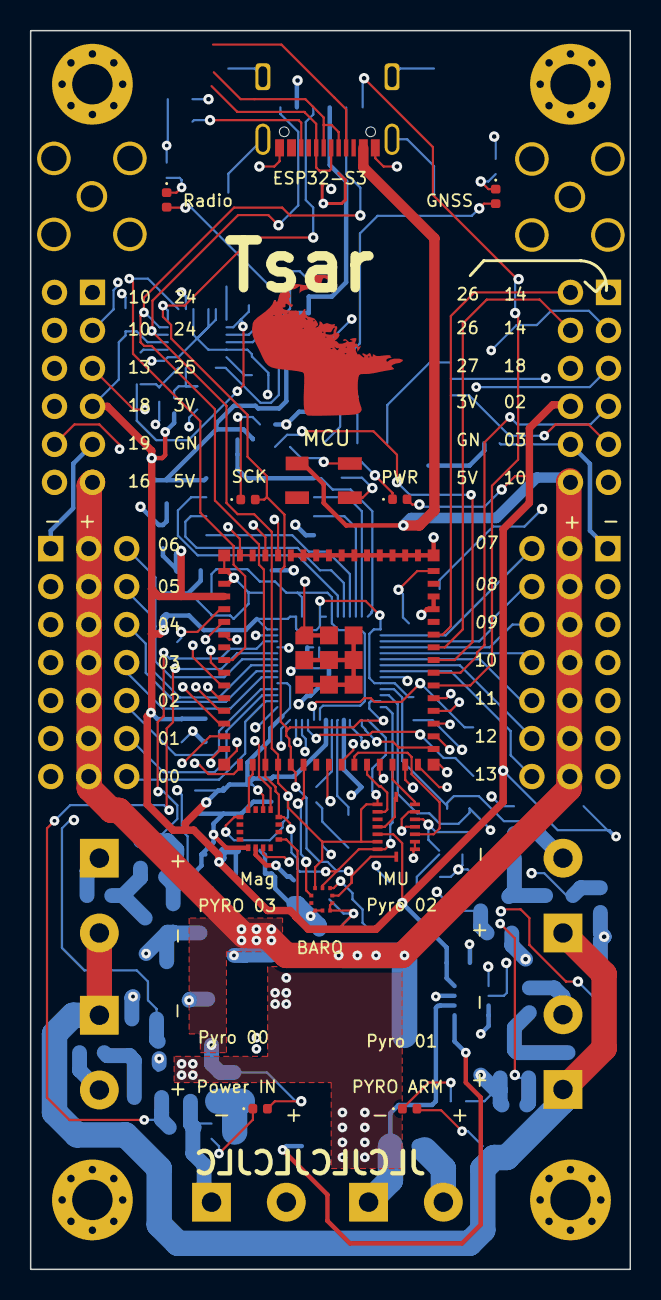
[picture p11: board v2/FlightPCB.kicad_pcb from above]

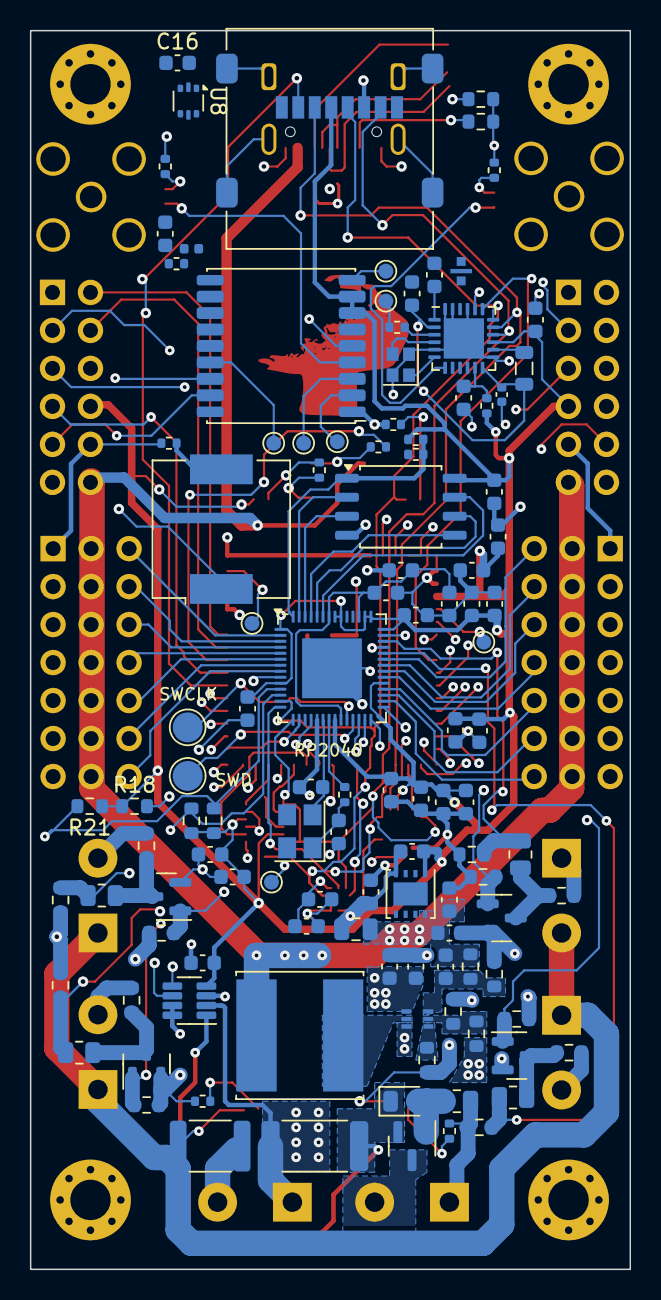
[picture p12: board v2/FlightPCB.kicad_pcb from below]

Board: 4 copper layers, 40.1 x 82.8 mm, 142 parts (114 on the bottom side), 124 nets.

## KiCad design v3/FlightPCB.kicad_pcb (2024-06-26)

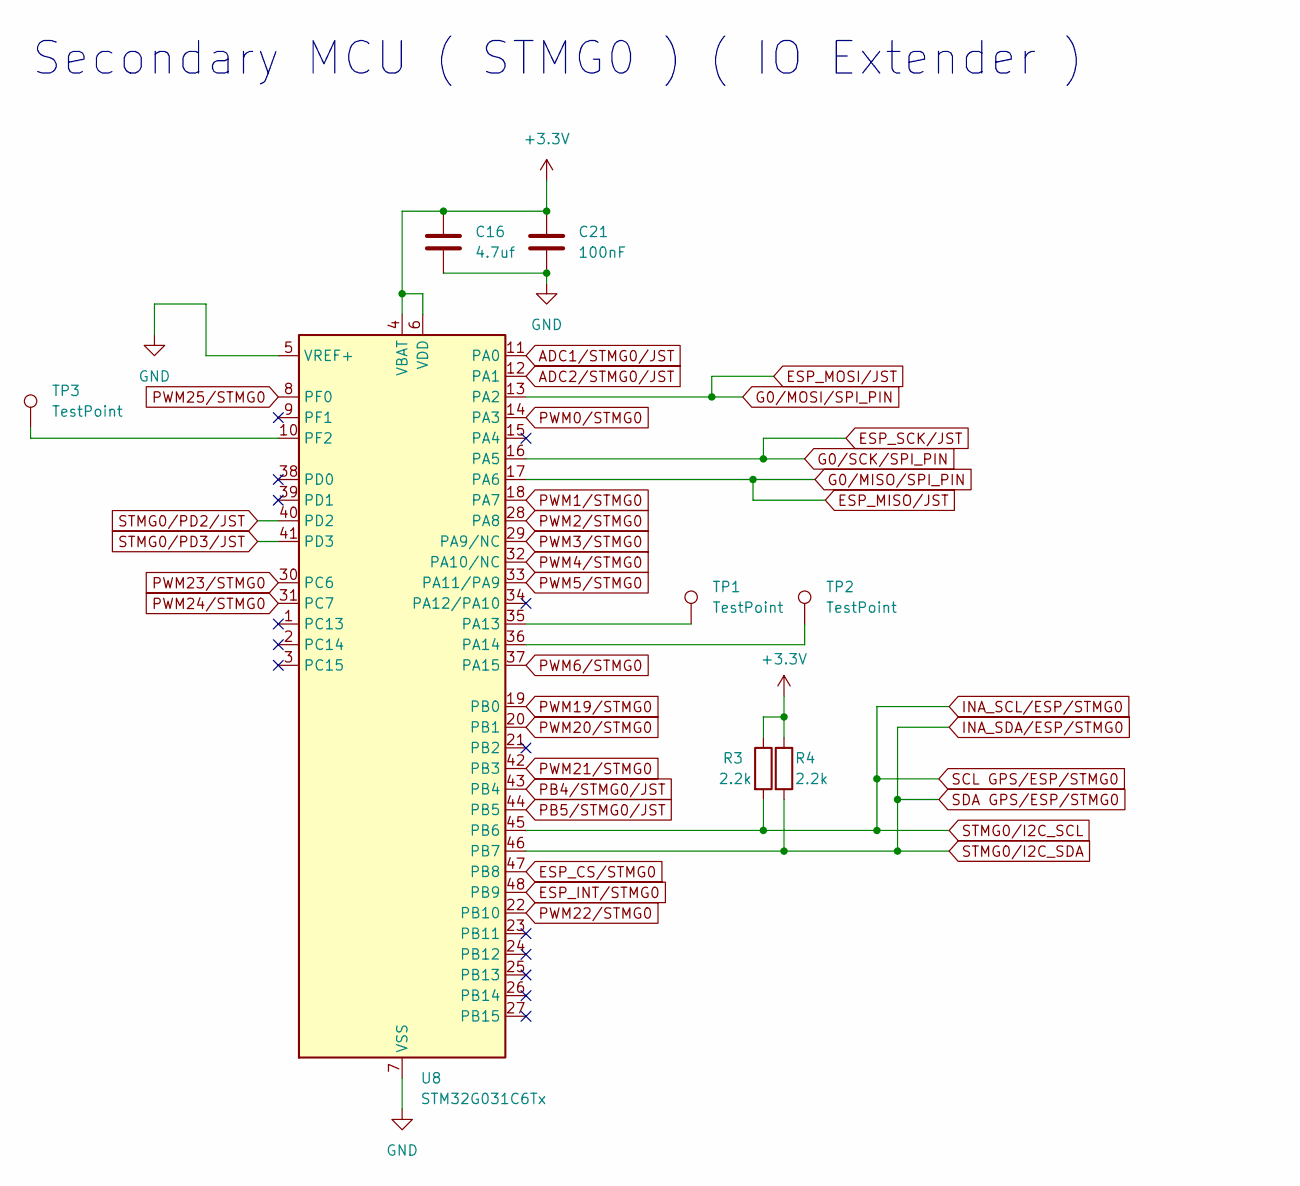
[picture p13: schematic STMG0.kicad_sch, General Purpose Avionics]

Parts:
C16: 4.7uf; C_0402_1005Metric
C21: 100nF; C_0402_1005Metric
R3, R4: 2.2k; R_0603_1608Metric
TP1, TP2, TP3: TestPoint; TestPoint_Pad_D1.0mm
U8: STM32G031C6Tx; LQFP-48_7x7mm_P0.5mm

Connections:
+3.3V: C16.1, C21.1, R3.1, R4.1, U8.4 (VBAT), U8.6 (VDD); also elsewhere on the board
ADC1/STMG0/JST: U8.11 (PA0); also elsewhere on the board
ADC2/STMG0/JST: U8.12 (PA1); also elsewhere on the board
BARO_MISO/ESP: U8.17 (PA6); also elsewhere on the board
BARO_MOSI/ESP: U8.13 (PA2); also elsewhere on the board
BARO_SCK/ESP: U8.16 (PA5); also elsewhere on the board
BatteryTerminal-: C16.2, C21.2, U8.5 (VREF+), U8.7 (VSS); also elsewhere on the board
ESP_CS/STMG0: U8.47 (PB8); also elsewhere on the board
ESP_INT/STMG0: U8.48 (PB9); also elsewhere on the board
ESP_SCL/Headers/JST: R3.2, U8.45 (PB6); also elsewhere on the board
ESP_SDA/Headers/JST: R4.2, U8.46 (PB7); also elsewhere on the board
unnamed: TP1.1, U8.35 (PA13)
unnamed: TP2.1, U8.36 (PA14)
unnamed: TP3.1, U8.10 (PF2)
PB4/STMG0/JST: U8.43 (PB4); also elsewhere on the board
PB5/STMG0/JST: U8.44 (PB5); also elsewhere on the board
PWM0/STMG0: U8.14 (PA3); also elsewhere on the board
PWM1/STMG0: U8.18 (PA7); also elsewhere on the board
PWM2/STMG0: U8.28 (PA8); also elsewhere on the board
PWM3/STMG0: U8.29 (PA9/NC); also elsewhere on the board
PWM4/STMG0: U8.32 (PA10/NC); also elsewhere on the board
PWM5/STMG0: U8.33 (PA11/PA9); also elsewhere on the board
PWM6/STMG0: U8.37 (PA15); also elsewhere on the board
PWM19/STMG0: U8.19 (PB0); also elsewhere on the board
PWM20/STMG0: U8.20 (PB1); also elsewhere on the board
PWM21/STMG0: U8.42 (PB3); also elsewhere on the board
PWM22/STMG0: U8.22 (PB10); also elsewhere on the board
PWM23/STMG0: U8.30 (PC6); also elsewhere on the board
PWM24/STMG0: U8.31 (PC7); also elsewhere on the board
PWM25/STMG0: U8.8 (PF0); also elsewhere on the board
STMG0/PD2/JST: U8.40 (PD2); also elsewhere on the board
STMG0/PD3/JST: U8.41 (PD3); also elsewhere on the board

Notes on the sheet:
Secondary MCU ( STMG0 ) ( IO Extender )

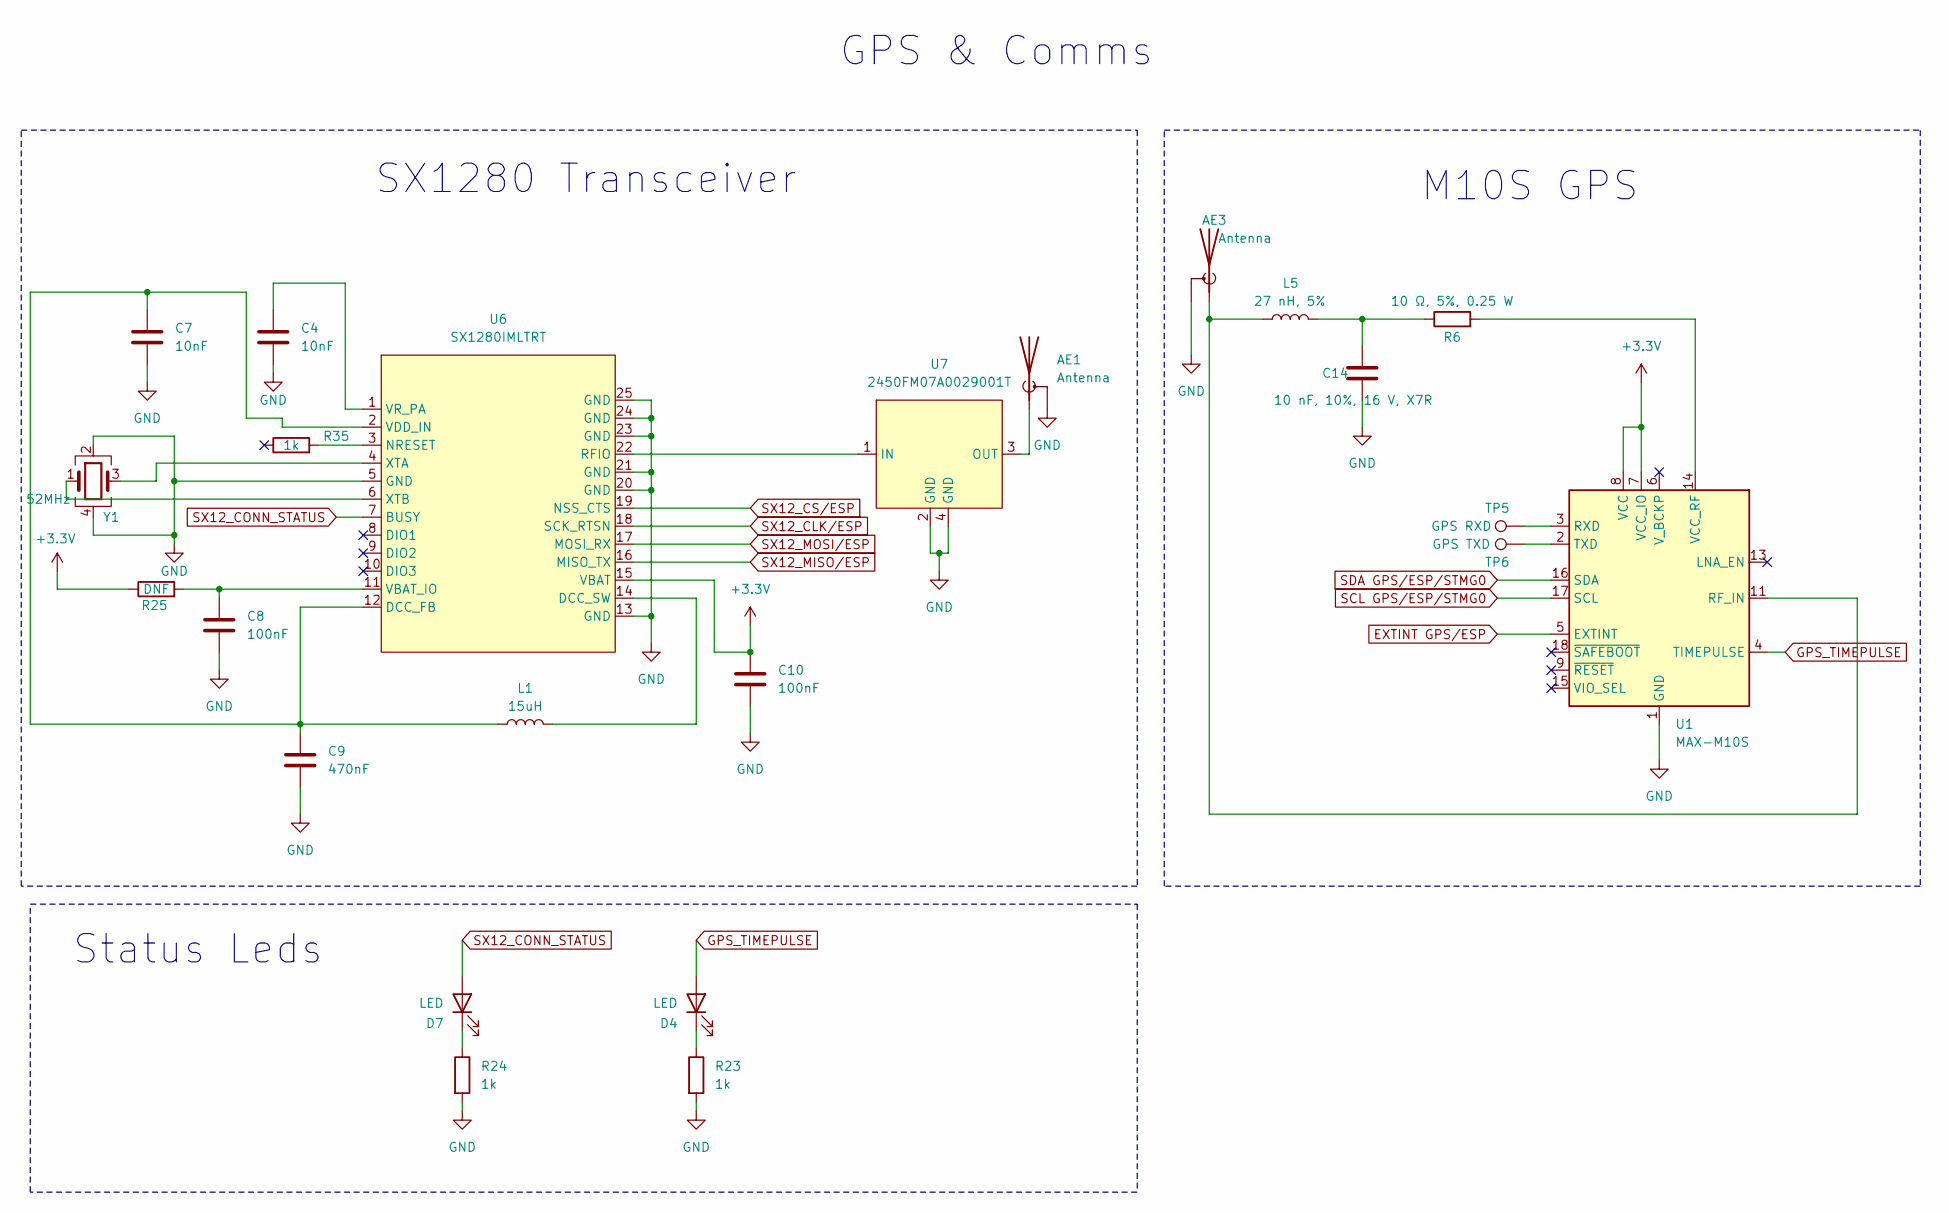
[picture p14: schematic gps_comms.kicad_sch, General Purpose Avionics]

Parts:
AE1, AE3: Antenna; SMA_Amphenol_901-144_Vertical
C4, C7: 10nF; C_0603_1608Metric
C8, C10: 100nF; C_0603_1608Metric
C9: 470nF; C_0402_1005Metric
C14: 10 nF, 10%, 16 V, X7R; C_0603_1608Metric
D4, D7: LED; LED_0402_1005Metric
L1: 15uH; L_0805_2012Metric
L5: 27 nH, 5%; L_0402_1005Metric
R6: 10 Ω, 5%, 0.25 W; R_0402_1005Metric
R23, R24, R35: 1k; R_0402_1005Metric
R25: DNF; R_0402_1005Metric
TP5: GPS RXD; TestPoint_Pad_D1.0mm
TP6: GPS TXD; TestPoint_Pad_D1.0mm
U1: MAX-M10S; ublox_MAX
U6: SX1280IMLTRT; QFN-24-1EP_4x4mm_P0.5mm_EP2.7x2.7mm
U7: 2450FM07A0029001T
Y1: 52MHz; Crystal_SMD_2016-4Pin_2.0x1.6mm

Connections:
+3.3V: C10.1, R25.1, U1.7 (VCC_IO), U1.8 (VCC), U6.15 (VBAT); also elsewhere on the board
BARO_MISO/ESP: U6.16 (MISO_TX); also elsewhere on the board
BARO_MOSI/ESP: U6.17 (MOSI_RX); also elsewhere on the board
BARO_SCK/ESP: U6.18 (SCK_RTSN); also elsewhere on the board
BatteryTerminal-: AE1.2 (Shield), AE3.2 (Shield), C4.2, C7.2, C8.2, C9.2, C10.2, C14.1, R23.2, R24.2, U1.1 (GND), U1.10 (GND), U1.12 (GND), U6.5 (GND), U6.13 (GND), U6.20 (GND), U6.21 (GND), U6.23 (GND), U6.24 (GND), U6.25 (GND), U7.2 (GND), U7.4 (GND), Y1.2, Y1.4; also elsewhere on the board
ESP_SCL/Headers/JST: U1.17 (SCL); also elsewhere on the board
ESP_SDA/Headers/JST: U1.16 (SDA); also elsewhere on the board
EXTINT GPS/ESP: U1.5 (EXTINT); also elsewhere on the board
GPS_TIMEPULSE: D4.2 (A), U1.4 (TIMEPULSE)
unnamed: AE1.1 (A), U7.3 (OUT)
unnamed: AE3.1 (A), L5.1, U1.11 (RF_IN)
unnamed: C14.2, L5.2, R6.1
unnamed: D4.1 (K), R23.1
unnamed: D7.1 (K), R24.1
unnamed: TP5.1, U1.3 (RXD)
unnamed: TP6.1, U1.2 (TXD)
unnamed: R6.2, U1.14 (VCC_RF)
unnamed: C7.1, C9.1, L1.1, U6.2 (VDD_IN), U6.12 (DCC_FB)
unnamed: L1.2, U6.14 (DCC_SW)
unnamed: R35.2, U6.3 (NRESET)
unnamed: U6.22 (RFIO), U7.1 (IN)
unnamed: C8.1, R25.2, U6.11 (VBAT_IO)
unnamed: C4.1, U6.1 (VR_PA)
unnamed: U6.4 (XTA), Y1.3
unnamed: U6.6 (XTB), Y1.1
SX12_CONN_STATUS: D7.2 (A), U6.7 (BUSY)
SX12_CS/ESP: U6.19 (NSS_CTS); also elsewhere on the board

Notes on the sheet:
GPS & Comms
M10S GPS
Status Leds
SX1280 Transceiver

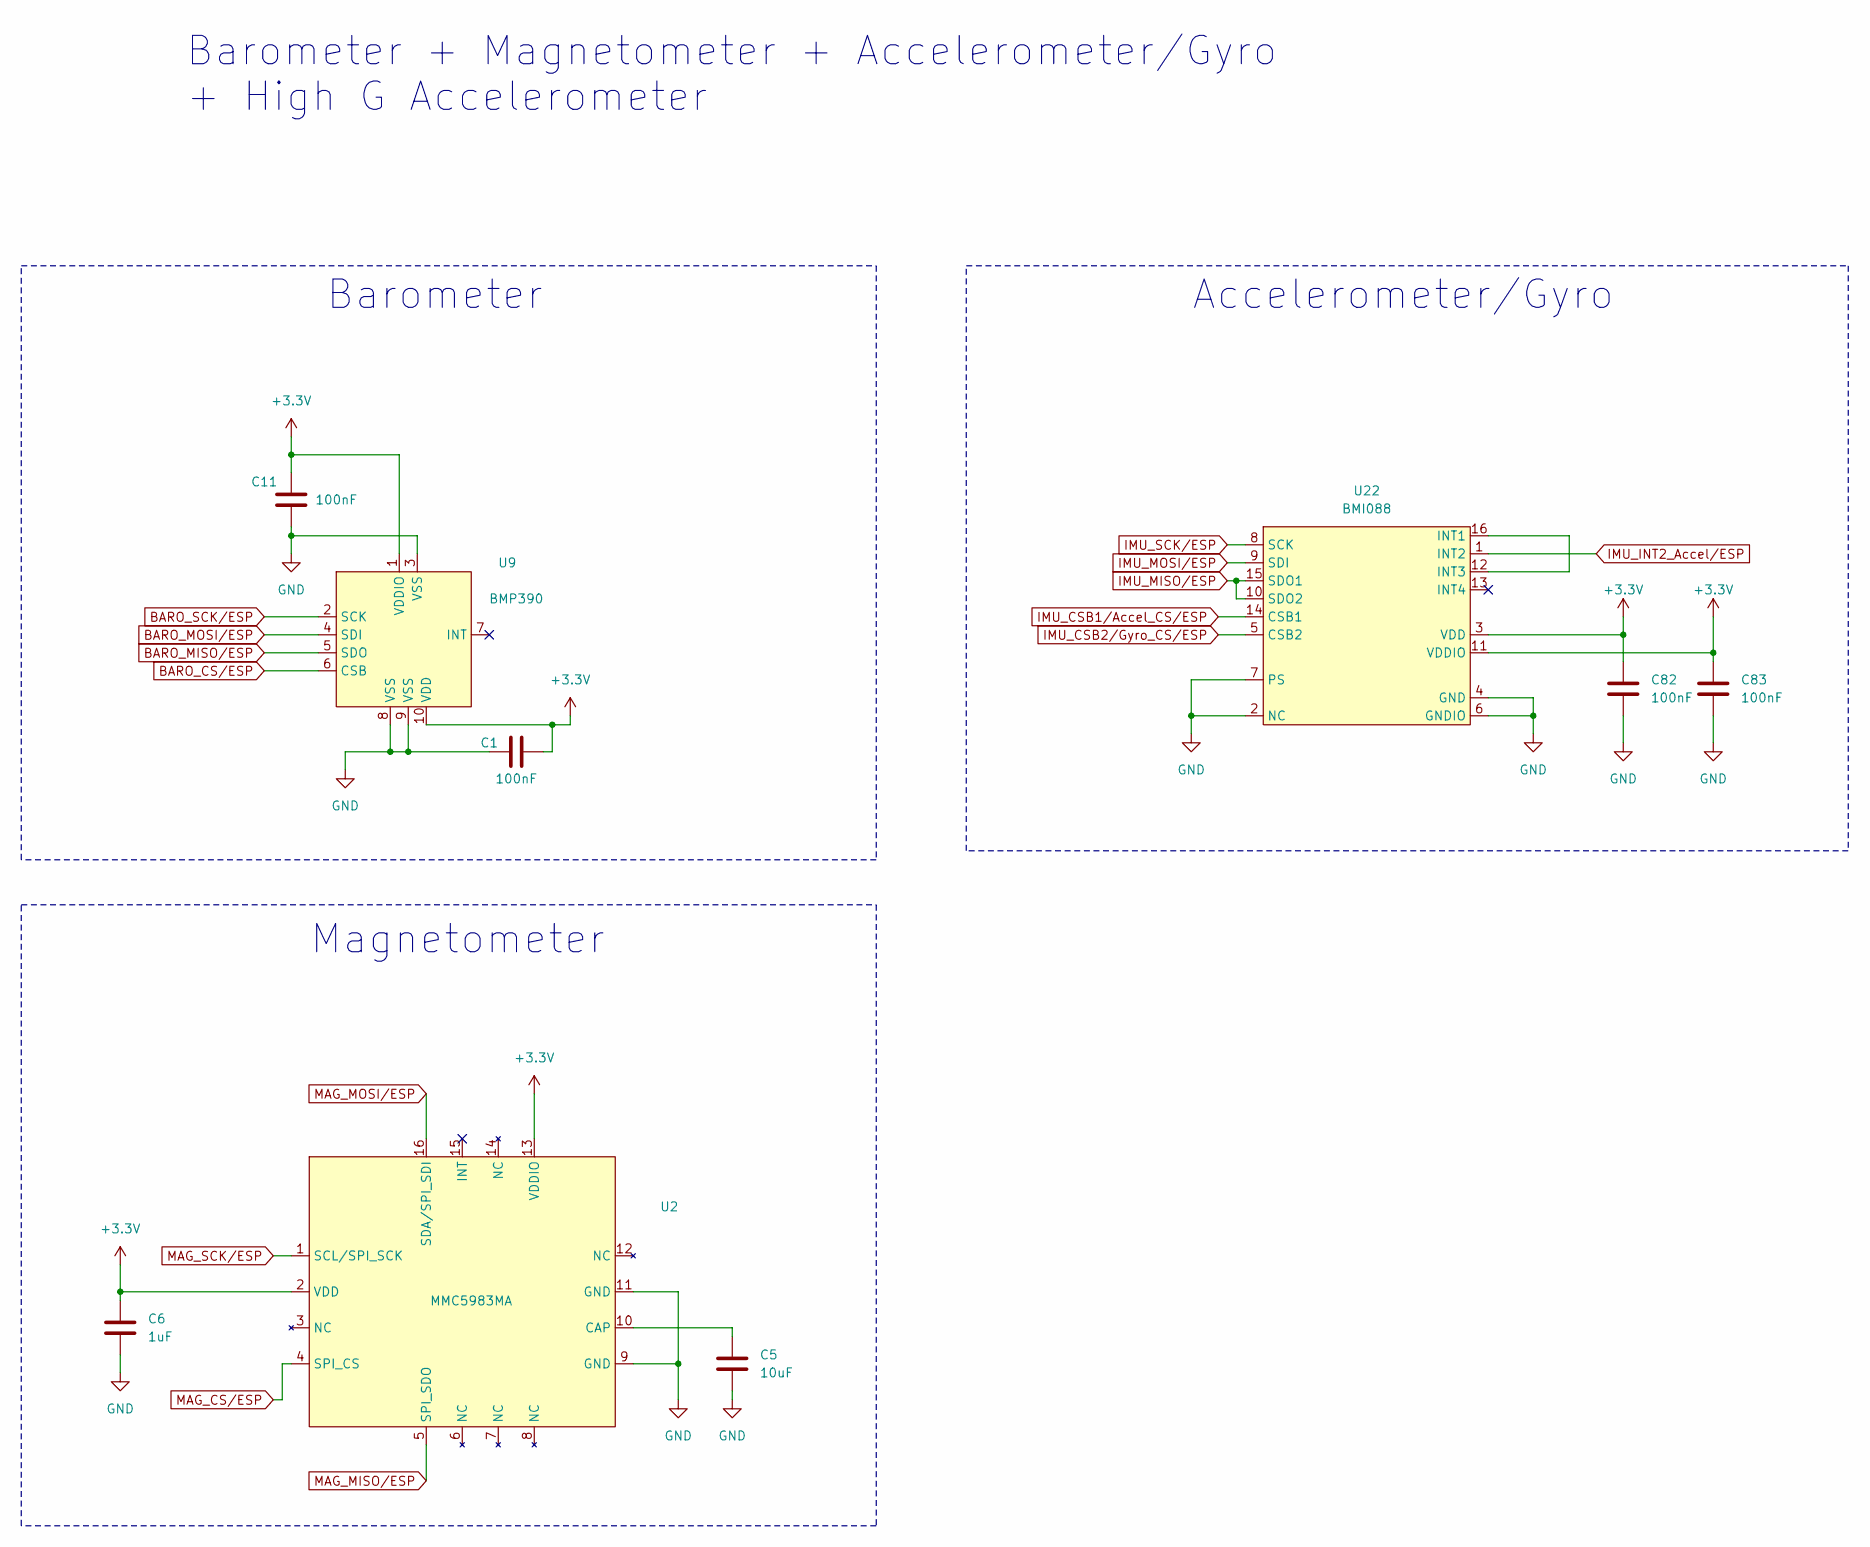
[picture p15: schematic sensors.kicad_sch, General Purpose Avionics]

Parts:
C1, C11, C82, C83: 100nF; C_0603_1608Metric
C5: 10uF; C_0603_1608Metric
C6: 1uF; C_0603_1608Metric
U2: MMC5983MA
U9: BMP390
U22: BMI088

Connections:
+3.3V: C1.2, C6.1, C11.2, C82.1, C83.1, U2.2 (VDD), U2.13 (VDDIO), U9.1 (VDDIO), U9.10 (VDD), U22.3 (VDD), U22.11 (VDDIO); also elsewhere on the board
BARO_CS/ESP: U9.6 (CSB); also elsewhere on the board
BARO_MISO/ESP: U2.5 (SPI_SDO), U9.5 (SDO), U22.10 (SDO2), U22.15 (SDO1); also elsewhere on the board
BARO_MOSI/ESP: U2.16 (SDA/SPI_SDI), U9.4 (SDI), U22.9 (SDI); also elsewhere on the board
BARO_SCK/ESP: U2.1 (SCL/SPI_SCK), U9.2 (SCK), U22.8 (SCK); also elsewhere on the board
BatteryTerminal-: C1.1, C5.2, C6.2, C11.1, C82.2, C83.2, U2.9 (GND), U2.11 (GND), U9.3 (VSS), U9.8 (VSS), U9.9 (VSS), U22.2 (NC), U22.4 (GND), U22.6 (GNDIO), U22.7 (PS); also elsewhere on the board
IMU_CSB1/Accel_CS/ESP: U22.14 (CSB1); also elsewhere on the board
IMU_CSB2/Gyro_CS/ESP: U22.5 (CSB2); also elsewhere on the board
IMU_INT2_Accel/ESP: U22.1 (INT2); also elsewhere on the board
MAG_CS/ESP: U2.4 (SPI_CS); also elsewhere on the board
unnamed: C5.1, U2.10 (CAP)
unnamed: U22.12 (INT3), U22.16 (INT1)

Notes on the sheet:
Accelerometer/Gyro
Magnetometer
Barometer
Barometer + Magnetometer + Accelerometer/Gyro + High G Accelerometer


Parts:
C2, C3: 4.7uF; C_0603_1608Metric
C15: 10uF; C_0603_1608Metric
C17, C18, C20, C23: 100nF; C_0603_1608Metric
C19: 22uF; C_0805_2012Metric
D1: PDZ10B, 115 10V 400mW; D_0805_2012Metric
D2, D3: LED; LED_0402_1005Metric
H1, H2, H3, H4: MountingHole_Pad; MountingHole_2.7mm_M2.5_Pad_Via
L2: 4.7uH; L_Cenker_CKCS8040
Q1: Si2369BDS MOSFET P-CH 30V 5.6A/7.5A; SOT-23
R5: 100k; R_0805_2012Metric
R8: 0.01; R_2512_6332Metric
R10: 113k; R_0603_1608Metric
R13, R30: 30k; R_0603_1608Metric
R15, R17: 1k; R_0402_1005Metric
R28: 10k; R_0603_1608Metric
R29: 220k; R_0603_1608Metric
U4: TPS564257DRLR; SOT50P160X60-6N; PARTREV A
U5: AP7361C-33FGE-7; MLF-8-1EP_3x3mm_P0.65mm_EP1.55x2.3mm
U11: INA219AxDCN; SOT-23-8

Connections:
+3.3V: C3.1, C23.2, D2.2 (A), U5.1 (OUT), U11.4 (VS); also elsewhere on the board
+5V: C2.1, C18.1, C19.1, C20.1, D3.2 (A), L2.2, R28.1, R29.1, U5.8 (VIN); also elsewhere on the board
BatteryTerminal+: Q1.3 (D); also elsewhere on the board
BatteryTerminal-: C2.2, C3.2, C15.2, C17.2, C19.2, C20.2, C23.1, H1.1, H2.1, H3.1, H4.1, R5.2, R13.2, R15.2, R17.2, R30.2, U4.3 (GND), U5.4 (GND), U11.3 (GND), U11.7 (A0), U11.8 (A1); also elsewhere on the board
ESP_SCL/Headers/JST: U11.5 (SCL); also elsewhere on the board
ESP_SDA/Headers/JST: U11.6 (SDA); also elsewhere on the board
INA+: D1.1 (K), Q1.2 (S), R8.1, U11.1 (IN+)
INA-: C15.1, C17.1, R8.2, R10.1, U4.1 (VIN), U11.2 (IN-); also elsewhere on the board
unnamed: D1.2 (A), Q1.1 (G), R5.1
unnamed: D2.1 (K), R15.1
unnamed: D3.1 (K), R17.1
unnamed: R10.2, R13.1, U4.5 (EN)
unnamed: C18.2, R29.2, R30.1, U4.6 (FB)
unnamed: R28.2, U4.4 (PG)
unnamed: L2.1, U4.2 (SW)

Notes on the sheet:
INA219AIDCNR
3.3V LDO
SRU1048-4R7Y SPM6530T-4R7M IHLP2525CZER4R7M01
Voltage and Current Sensor
3.3V 1A
Reverse Voltage Protection
5.12V 4A
LEDs & Mounting Holes
Power Distribution
Buck Converter
usb-c vbus here?


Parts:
J2, J15: TerminalBlock; TerminalBlock_Phoenix_PT-1,5-2-5.0-H_1x02_P5.00mm_Horizontal
J3, J16: Conn_01x04; JST_SH_BM04B-SRSS-TB_1x04-1MP_P1.00mm_Vertical
J4, J5, J7, J10, J12, J13: Conn_01x04; Hirose_DF13-04P-1.25DSA_1x04_P1.25mm_Vertical
J6, J9: Conn_01x06; Hirose_DF13-06P-1.25DSA_1x06_P1.25mm_Vertical
J8: USB_C_Receptacle; USB_C_Receptacle_GCT_USB4105-xx-A_16P_TopMnt_Horizontal
J11: PinHeader_3x05_P2.54mm_Vertical_Left
J14: PinHeader_3x05_P2.54mm_Vertical_Right
JP2: VBUS; SolderJumper-2_P1.3mm_Open_TrianglePad1.0x1.5mm
JP3, JP4: SolderJumper_3_Bridged12; SolderJumper-3_P1.3mm_Bridged12_Pad1.0x1.5mm_NumberLabels
R14, R16: 5.1k; R_0603_1608Metric
U12: USBLC6-2SC6; SOT-23-6

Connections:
+5V: J3.3, J4.1, J5.1, J6.1, J7.1, J9.1, J10.1, J12.1, J13.1, J16.3, JP2.2 (B), JP3.1 (A), JP4.1 (A), U12.5 (VBUS); also elsewhere on the board
ADC1/STMG0/JST: J4.3; also elsewhere on the board
ADC2/STMG0/JST: J4.2; also elsewhere on the board
BARO_MISO/ESP: J6.3; also elsewhere on the board
BARO_MOSI/ESP: J6.4; also elsewhere on the board
BARO_SCK/ESP: J6.2; also elsewhere on the board
BatteryTerminal+: J2.2; also elsewhere on the board
BatteryTerminal-: J2.1, J3.4, J4.4, J5.4, J6.6, J7.4, J8.A1 (GND), J8.A12 (GND), J8.B1 (GND), J8.B12 (GND), J8.S1 (SHIELD), J9.6, J10.4, J11.1 (GND), J11.2 (GND), J11.3 (GND), J11.4 (GND), J11.5 (GND), J11.6 (GND), J11.7 (GND), J12.4, J13.4, J14.1 (GND), J14.2 (GND), J14.3 (GND), J14.4 (GND), J14.5 (GND), J14.6 (GND), J14.7 (GND), J15.2, J16.4, R14.1, R16.1, U12.2 (GND); also elsewhere on the board
ESP32_D+: U12.4 (I/O2); also elsewhere on the board
ESP32_D-: U12.6 (I/O1); also elsewhere on the board
ESP_IO5/Headers: J12.2; also elsewhere on the board
ESP_IO6/Headers: J12.3; also elsewhere on the board
ESP_IO7/Headers: J16.1; also elsewhere on the board
ESP_IO8/Headers: J16.2; also elsewhere on the board
ESP_IO9/Headers/JST: J9.5; also elsewhere on the board
ESP_IO11/Headers/JST: J9.4; also elsewhere on the board
ESP_IO12/Headers/JST: J9.2; also elsewhere on the board
ESP_IO13/Headers/JST: J9.3; also elsewhere on the board
ESP_IO36/Headers: J10.3; also elsewhere on the board
ESP_IO37/Headers: J10.2; also elsewhere on the board
ESP_RX/Headers: J7.3; also elsewhere on the board
ESP_SCL/Headers/JST: J3.2; also elsewhere on the board
ESP_SDA/Headers/JST: J3.1; also elsewhere on the board
ESP_TX/Headers: J7.2; also elsewhere on the board
INA-: J15.1, JP3.3 (B), JP4.3 (B); also elsewhere on the board
JST_CONN_CS/JST: J6.5; also elsewhere on the board
unnamed: J8.A5 (CC1), R16.2
unnamed: J8.B5 (CC2), R14.2
unnamed: J8.A6 (D+), J8.B6 (D+), U12.3 (I/O2)
unnamed: J8.A7 (D-), J8.B7 (D-), U12.1 (I/O1)
unnamed: J8.A4 (VBUS), J8.A9 (VBUS), J8.B4 (VBUS), J8.B9 (VBUS), JP2.1 (A)
unnamed: J11.8 (5V), J11.9 (5V), J11.10 (5V), J11.11 (5V), J11.12 (5V), J11.13 (5V), J11.14 (5V), JP3.2 (C)
unnamed: J14.8 (5V), J14.9 (5V), J14.10 (5V), J14.11 (5V), J14.12 (5V), J14.13 (5V), J14.14 (5V), JP4.2 (C)
PB4/STMG0/JST: J13.2; also elsewhere on the board
PB5/STMG0/JST: J13.3; also elsewhere on the board
PWM0/STMG0: J11.19 (SIG); also elsewhere on the board
PWM1/STMG0: J11.18 (SIG); also elsewhere on the board
PWM2/STMG0: J14.15 (SIG); also elsewhere on the board
PWM3/STMG0: J14.16 (SIG); also elsewhere on the board
PWM4/STMG0: J14.19 (SIG); also elsewhere on the board
PWM5/STMG0: J14.20 (SIG); also elsewhere on the board
PWM6/STMG0: J14.21 (SIG); also elsewhere on the board
PWM19/STMG0: J11.17 (SIG); also elsewhere on the board
PWM20/STMG0: J11.16 (SIG); also elsewhere on the board
PWM21/STMG0: J11.21 (SIG); also elsewhere on the board
PWM22/STMG0: J11.15 (SIG); also elsewhere on the board
PWM23/STMG0: J14.17 (SIG); also elsewhere on the board
PWM24/STMG0: J14.18 (SIG); also elsewhere on the board
PWM25/STMG0: J11.20 (SIG); also elsewhere on the board
STMG0/PD2/JST: J5.2; also elsewhere on the board
STMG0/PD3/JST: J5.3; also elsewhere on the board

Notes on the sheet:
Input 6V - 16V
ESP32-USBC
Power Input + Pyro Arm

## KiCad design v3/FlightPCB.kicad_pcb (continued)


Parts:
BZ1: Buzzer; Buzzer_CUI_CPT-9019S-SMT
C12: 100nF; C_0603_1608Metric
C13: 10uF; C_0603_1608Metric
D6: LED; LED_0402_1005Metric
D8: ESP Status; IN-PI22TAT5R5G5B
J1: Micro_SD_Card; microSD_HC_Molex_47219-2001
R20, R22: 1k; R_0402_1005Metric
R26: DNF; R_0402_1005Metric
TP8: Bootio; TestPoint_Pad_D1.0mm
TP9: EN; TestPoint_Pad_D1.0mm
U10: ESP32-S3-MINI-1U; ESP32-S2-MINI-1U

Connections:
+3.3V: C12.1, C13.1, J1.4 (VDD), U10.3 (3V3); also elsewhere on the board
+5V: D8.3 (A2); also elsewhere on the board
/esp32_s3/SDCard_CS: J1.2 (DAT3/CD), U10.36 (IO40)
BARO_CS/ESP: U10.21 (IO17); also elsewhere on the board
BARO_MISO/ESP: J1.7 (DAT0), U10.19 (IO15); also elsewhere on the board
BARO_MOSI/ESP: J1.3 (CMD), U10.18 (IO14); also elsewhere on the board
BARO_SCK/ESP: D6.2 (A), J1.5 (CLK), U10.20 (IO16); also elsewhere on the board
BatteryTerminal-: C12.2, C13.2, D8.1 (A1), J1.6 (VSS), J1.9 (SHIELD), R20.2, R26.2, U10.1 (GND), U10.2 (GND), U10.42 (GND), U10.43 (GND), U10.46 (GND), U10.47 (GND), U10.48 (GND), U10.49 (GND), U10.50 (GND), U10.51 (GND), U10.52 (GND), U10.53 (GND), U10.54 (GND), U10.55 (GND), U10.56 (GND), U10.57 (GND), U10.58 (GND), U10.59 (GND), U10.60 (GND), U10.61 (GND), U10.62 (GND), U10.63 (GND), U10.64 (GND), U10.65 (GND); also elsewhere on the board
ESP32_D+: U10.24 (IO20); also elsewhere on the board
ESP32_D-: U10.23 (IO19); also elsewhere on the board
ESP_CS/STMG0: U10.31 (IO35); also elsewhere on the board
ESP_INT/STMG0: U10.27 (IO47); also elsewhere on the board
ESP_IO5/Headers: U10.9 (IO5); also elsewhere on the board
ESP_IO6/Headers: U10.10 (IO6); also elsewhere on the board
ESP_IO7/Headers: U10.11 (IO7); also elsewhere on the board
ESP_IO8/Headers: U10.12 (IO8); also elsewhere on the board
ESP_IO9/Headers/JST: U10.13 (IO9); also elsewhere on the board
ESP_IO11/Headers/JST: U10.15 (IO11); also elsewhere on the board
ESP_IO12/Headers/JST: U10.16 (IO12); also elsewhere on the board
ESP_IO13/Headers/JST: U10.17 (IO13); also elsewhere on the board
ESP_IO36/Headers: U10.32 (IO36); also elsewhere on the board
ESP_IO37/Headers: U10.33 (IO37); also elsewhere on the board
ESP_RX/Headers: U10.34 (IO38); also elsewhere on the board
ESP_SCL/Headers/JST: U10.6 (IO2); also elsewhere on the board
ESP_SDA/Headers/JST: U10.5 (IO1); also elsewhere on the board
ESP_TX/Headers: U10.35 (IO39); also elsewhere on the board
EXTINT GPS/ESP: U10.29 (IO34); also elsewhere on the board
IMU_CSB1/Accel_CS/ESP: U10.26 (IO26); also elsewhere on the board
IMU_CSB2/Gyro_CS/ESP: U10.25 (IO21); also elsewhere on the board
IMU_INT2_Accel/ESP: U10.28 (IO33); also elsewhere on the board
JST_CONN_CS/JST: U10.7 (IO3); also elsewhere on the board
MAG_CS/ESP: U10.14 (IO10); also elsewhere on the board
unnamed: BZ1.1 (+), U10.30 (IO48)
unnamed: BZ1.2 (-), R26.1
unnamed: D6.1 (K), R20.1
unnamed: D8.2 (K1), R22.2
unnamed: TP9.1, U10.45 (EN)
unnamed: TP8.1, U10.4 (IO0)
unnamed: R22.1, U10.38 (IO42)
SX12_CS/ESP: U10.8 (IO4); also elsewhere on the board

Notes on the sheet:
Status + Buzzer
ESP32-S3



Board: 4 copper layers, 40.1 x 82.8 mm, 99 parts (68 on the bottom side), 99 nets.

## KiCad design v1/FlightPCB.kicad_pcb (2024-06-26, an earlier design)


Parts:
AE1, AE3: Antenna; SMA_Amphenol_901-144_Vertical
C4, C7: 10nF; C_0402_1005Metric
C8, C10: 100nF; C_0402_1005Metric
C9: 470nF; C_0402_1005Metric
C14: 10 nF, 10%, 16 V, X7R; C_0603_1608Metric
L1: 15uH; L_0805_2012Metric
L5: 27 nH, 5%; L_0402_1005Metric
R6: 10 Ω, 5%, 0.25 W; R_0402_1005Metric
R25: 0; R_0402_1005Metric
R26, R31, R33, R34, R35: 1k; R_0402_1005Metric
TP1: VIO_SEL; TestPoint_Pad_D1.0mm
TP3: Reset; TestPoint_Pad_D1.0mm
TP4: TestPoint; TestPoint_Pad_D1.0mm
TP5: GPS RXD; TestPoint_Pad_D1.0mm
TP6: GPS TXD; TestPoint_Pad_D1.0mm
U1: MAX-M10S; ublox_MAX
U6: SX1280IMLTRT; QFN-24-1EP_4x4mm_P0.5mm_EP2.7x2.7mm
U7: 2450FM07A0029001T
Y1: 52MHz; Crystal_SMD_2016-4Pin_2.0x1.6mm

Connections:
+3.3V: C10.1, R25.1, U1.7 (VCC_IO), U1.8 (VCC), U6.15 (VBAT); also elsewhere on the board
BatteryTerminal-: AE1.2 (Shield), AE3.2 (Shield), C4.2, C7.2, C8.2, C9.2, C10.2, C14.1, U1.1 (GND), U1.10 (GND), U1.12 (GND), U6.5 (GND), U6.13 (GND), U6.20 (GND), U6.21 (GND), U6.23 (GND), U6.24 (GND), U6.25 (GND), U7.2 (GND), U7.4 (GND), Y1.2, Y1.4; also elsewhere on the board
EXTINT GPS/RPI2040: U1.5 (EXTINT); also elsewhere on the board
GPS_TIMEPULSE: U1.4 (TIMEPULSE); also elsewhere on the board
INA_SCL_RPI2040: U1.17 (SCL); also elsewhere on the board
INA_SDA_RPI2040: U1.16 (SDA); also elsewhere on the board
unnamed: AE1.1 (A), U7.3 (OUT)
unnamed: AE3.1 (A), L5.1, U1.11 (RF_IN)
unnamed: C14.2, L5.2, R6.1
unnamed: R35.1, TP4.1
unnamed: TP5.1, U1.3 (RXD)
unnamed: TP6.1, U1.2 (TXD)
unnamed: R6.2, U1.14 (VCC_RF)
unnamed: TP1.1, U1.15 (VIO_SEL)
unnamed: TP3.1, U1.9 (~RESET)
unnamed: C7.1, C9.1, L1.1, U6.2 (VDD_IN), U6.12 (DCC_FB)
unnamed: L1.2, U6.14 (DCC_SW)
unnamed: R34.1, U6.16 (MISO_TX)
unnamed: R33.1, U6.17 (MOSI_RX)
unnamed: R35.2, U6.3 (NRESET)
unnamed: R26.1, U6.19 (NSS_CTS)
unnamed: U6.22 (RFIO), U7.1 (IN)
unnamed: R31.1, U6.18 (SCK_RTSN)
unnamed: C8.1, R25.2, U6.11 (VBAT_IO)
unnamed: C4.1, U6.1 (VR_PA)
unnamed: U6.4 (XTA), Y1.3
unnamed: U6.6 (XTB), Y1.1
RPI2040_GPIO16/MISO/SPI_PIN: R34.2; also elsewhere on the board
RPI2040_GPIO18/SCK/SPI_PIN: R31.2; also elsewhere on the board
RPI2040_GPIO19/MOSI/SPI_PIN: R33.2; also elsewhere on the board
SX12_CONN_STATUS: U6.7 (BUSY); also elsewhere on the board
SX12_CS/RPI2040: R26.2; also elsewhere on the board

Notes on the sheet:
M10S GPS
SX1280 Radio Module


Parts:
C1, C11, C82, C83: 100nF; C_0603_1608Metric
C5: 10uF; C_0805_2012Metric
C6: 1uF; C_0603_1608Metric
JP1: INT1; SolderJumper-2_P1.3mm_Bridged_Pad1.0x1.5mm
JP2: INT2; SolderJumper-2_P1.3mm_Bridged_Pad1.0x1.5mm
U2: MMC5983MA
U9: BMP390
U22: BMI088

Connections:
+3.3V: C1.2, C6.1, C11.2, C82.1, C83.1, U2.2 (VDD), U2.13 (VDDIO), U9.1 (VDDIO), U9.10 (VDD), U22.3 (VDD), U22.11 (VDDIO); also elsewhere on the board
BARO_CS/Teensy: U9.6 (CSB); also elsewhere on the board
BARO_MISO/Teensy: U2.5 (SPI_SDO), U9.5 (SDO), U22.10 (SDO2), U22.15 (SDO1); also elsewhere on the board
BARO_MOSI/Teensy: U2.16 (SDA/SPI_SDI), U9.4 (SDI), U22.9 (SDI); also elsewhere on the board
BARO_SCK/Teensy: U2.1 (SCL/SPI_SCK), U9.2 (SCK), U22.8 (SCK); also elsewhere on the board
BatteryTerminal-: C1.1, C5.2, C6.2, C11.1, C82.2, C83.2, U2.9 (GND), U2.11 (GND), U9.3 (VSS), U9.8 (VSS), U9.9 (VSS), U22.2 (NC), U22.4 (GND), U22.6 (GNDIO), U22.7 (PS); also elsewhere on the board
IMU_CSB1/Accel_CS/Teensy: U22.14 (CSB1); also elsewhere on the board
IMU_CSB2/Gyro_CS/Teensy: U22.5 (CSB2); also elsewhere on the board
IMU_INT2_Accel/Teensy: JP2.2 (B); also elsewhere on the board
MAG_CS/Teensy: U2.4 (SPI_CS); also elsewhere on the board
unnamed: JP1.1 (A), U22.16 (INT1)
unnamed: JP1.2 (B), U22.12 (INT3)
unnamed: JP2.1 (A), U22.1 (INT2)
unnamed: C5.1, U2.10 (CAP)

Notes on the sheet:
Barometer + Magnetometer + Accelerometer/Gyro + High G Accelerometer


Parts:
C2, C3: 4.7uF; C_0603_1608Metric
C15: 10uF; C_0805_2012Metric
C17, C18, C20, C23: 100nF; C_0603_1608Metric
C19: 22uF; C_0805_2012Metric
D1: PDZ10B, 115 10V 400mW; D_0805_2012Metric
L2: 4.7uH; L_0805_2012Metric
Q1: Si2369BDS MOSFET P-CH 30V 5.6A/7.5A; SOT-23
R5: 100k; R_0805_2012Metric
R8: 0.01; R_2512_6332Metric
R10: 113k; R_0603_1608Metric
R13, R30: 30k; R_0603_1608Metric
R28: 10k; R_0603_1608Metric
R29: 220k; R_0603_1608Metric
TP2: TestPoint; TestPoint_Pad_D1.0mm
U4: TPS564257DRLR; SOT50P160X60-6N; PARTREV A
U5: AP7361C-33FGE-7; MLF-8-1EP_3x3mm_P0.65mm_EP1.55x2.3mm
U11: INA219AxDCN; SOT-23-8

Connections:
+3.3V: C3.1, C23.2, U5.1 (OUT), U11.4 (VS); also elsewhere on the board
+5V: C2.1, C18.1, C19.1, C20.1, L2.2, R28.1, R29.1, U5.8 (VIN); also elsewhere on the board
BatteryTerminal+: Q1.3 (D); also elsewhere on the board
BatteryTerminal-: C2.2, C3.2, C15.2, C17.2, C19.2, C20.2, C23.1, R5.2, R13.2, R30.2, U4.3 (GND), U5.4 (GND), U11.3 (GND), U11.7 (A0), U11.8 (A1); also elsewhere on the board
INA+: D1.1 (K), Q1.2 (S), R8.1, U11.1 (IN+)
INA-: C15.1, C17.1, R8.2, R10.1, TP2.1, U4.1 (VIN), U11.2 (IN-)
INA_SCL_RPI2040: U11.5 (SCL); also elsewhere on the board
INA_SDA_RPI2040: U11.6 (SDA); also elsewhere on the board
unnamed: D1.2 (A), Q1.1 (G), R5.1
unnamed: R10.2, R13.1, U4.5 (EN)
unnamed: C18.2, R29.2, R30.1, U4.6 (FB)
unnamed: R28.2, U4.4 (PG)
unnamed: L2.1, U4.2 (SW)

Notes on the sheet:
Voltage and Current Sensor
3.3V 1A
Reverse Voltage Protection
5.2V 4A
Power Distribution


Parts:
C29, C30, C40, C42, C46, C47: 0.22uF; C_0402_1005Metric
C31: 2.2uF; C_0603_1608Metric
C33, C38, C43: 10uF; C_0603_1608Metric
C36, C37, C41: 4.7uF; C_0603_1608Metric
C45, C49: 10nF; C_0402_1005Metric
D12: BAT54C; SOT-23
IC1: MIMXRT1062DVJ6B; BGA196C80P14X14_1200X1200X152; Mouser Part Number 771-MIMXRT1062DVJ6B
J31: Micro_SD_Card; microSD_HC_Molex_47219-2001
L3: 120; L_0805_2012Metric
L4: 4.7uH; L_0805_2012Metric
R40: 470K; R_0603_1608Metric
R43, R44: 2.2k; R_0603_1608Metric
TP9: TestPoint; TestPoint_Pad_D1.0mm
TP12: PMIC_ON_REQ; TestPoint_Pad_D1.0mm
TP13: OnOFF; TestPoint_Pad_D1.0mm
TP14: VDD_USB_CAP; TestPoint_Pad_D1.0mm
U15: TLV75533PDBV; SOT-23-5

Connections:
+5V: C29.1, C30.1, IC1.N6 (USB_OTG1_VBUS), IC1.P6 (USB_OTG2_VBUS), U15.1 (IN); also elsewhere on the board
BARO_CS/Teensy: IC1.H11 (GPIO_AD_B1_13); also elsewhere on the board
BARO_MISO/Teensy: IC1.E7 (GPIO_B0_01); also elsewhere on the board
BARO_MOSI/Teensy: IC1.E8 (GPIO_B0_02); also elsewhere on the board
BARO_SCK/Teensy: IC1.D8 (GPIO_B0_03); also elsewhere on the board
BatteryTerminal-: C29.2, C30.2, C31.2, C33.2, C36.2, C37.2, C38.2, C40.2, C41.2, C42.2, C43.2, C45.2, C46.2, C47.2, C49.2, J31.6 (VSS), J31.9 (SHIELD), U15.2 (GND); also elsewhere on the board
IMU_CSB1/Accel_CS/Teensy: IC1.D14 (GPIO_B1_13); also elsewhere on the board
IMU_CSB2/Gyro_CS/Teensy: IC1.D11 (GPIO_B1_03); also elsewhere on the board
IMU_INT2_Accel/Teensy: IC1.D13 (GPIO_B1_12); also elsewhere on the board
MAG_CS/Teensy: IC1.C11 (GPIO_B1_02); also elsewhere on the board
unnamed: C38.1, C41.1, C47.1, IC1.L1 (DCDC_IN_1), IC1.L2 (DCDC_IN_2), L3.1
unnamed: IC1.M1 (DCDC_LP_1), IC1.M2 (DCDC_LP_2), L4.2
unnamed: C33.1, C37.1, C42.1, C49.1, IC1.F6 (VDD_SOC_IN_1), IC1.F7 (VDD_SOC_IN_2), IC1.F8 (VDD_SOC_IN_3), IC1.F9 (VDD_SOC_IN_4), IC1.G6 (VDD_SOC_IN_5), IC1.G9 (VDD_SOC_IN_6), IC1.H6 (VDD_SOC_IN_7), IC1.H9 (VDD_SOC_IN_8), IC1.J5 (DCDC_SENSE), IC1.J9 (VDD_SOC_IN_9), L4.1
unnamed: IC1.A7 (GPIO_EMC_40), TP9.1
unnamed: IC1.J4 (GPIO_SD_B0_00), J31.3 (CMD)
unnamed: IC1.J3 (GPIO_SD_B0_01), J31.5 (CLK)
unnamed: IC1.J1 (GPIO_SD_B0_02), J31.7 (DAT0)
unnamed: IC1.K1 (GPIO_SD_B0_03), J31.8 (DAT1)
unnamed: IC1.H2 (GPIO_SD_B0_04), J31.1 (DAT2)
unnamed: IC1.J2 (GPIO_SD_B0_05), J31.2 (DAT3/CD)
unnamed: IC1.M6 (ONOFF), TP13.1
unnamed: IC1.K7 (PMIC_ON_REQ), R40.1, TP12.1, U15.3 (EN)
unnamed: D12.3, IC1.M9 (VDD_SNVS_IN)
unnamed: C43.1, C46.1, D12.1, IC1.K8 (VDD_USB_CAP), TP14.1
PYRO1_SENSE: IC1.H12 (GPIO_AD_B1_12); also elsewhere on the board
PYRO1_TRIGGER/Teensy_21/A7: IC1.J13 (GPIO_AD_B1_11); also elsewhere on the board
PYRO2_SENSE: IC1.G12 (GPIO_AD_B1_14); also elsewhere on the board
PYRO2_TRIGGER/Teensy_22/A8: IC1.H13 (GPIO_AD_B1_08); also elsewhere on the board
PYRO3_SENSE: IC1.J14 (GPIO_AD_B1_15); also elsewhere on the board
PYRO3_TRIGGER/Teensy_23/A9: IC1.M13 (GPIO_AD_B1_09); also elsewhere on the board
PYRO4_SENSE: IC1.K12 (GPIO_AD_B1_05); also elsewhere on the board
PYRO4_TRIGGER/Teensy_41/A17: IC1.L12 (GPIO_AD_B1_04); also elsewhere on the board
TEENSY_0/RX1: IC1.G11 (GPIO_AD_B0_03); also elsewhere on the board
TEENSY_1/TX1: IC1.M11 (GPIO_AD_B0_02); also elsewhere on the board
TEENSY_2/PWM1: IC1.F2 (GPIO_EMC_04); also elsewhere on the board
TEENSY_3/PWM2: IC1.G5 (GPIO_EMC_05); also elsewhere on the board
TEENSY_4/PWM3: IC1.H5 (GPIO_EMC_06); also elsewhere on the board
TEENSY_5/PWM4: IC1.H3 (GPIO_EMC_08); also elsewhere on the board
TEENSY_6/PWM5: IC1.D9 (GPIO_B0_10); also elsewhere on the board
TEENSY_7/RX2/Serial_Pin: IC1.B11 (GPIO_B1_01); also elsewhere on the board
TEENSY_8/TX2/Serial_Pin: IC1.A11 (GPIO_B1_00); also elsewhere on the board
TEENSY_9/RPI2040_GPIO20_CS: IC1.A10 (GPIO_B0_11); also elsewhere on the board
TEENSY_10/CS/SPI_PIN: IC1.D7 (GPIO_B0_00); also elsewhere on the board
TEENSY_14/A0/PWM6: IC1.L11 (GPIO_AD_B1_02); also elsewhere on the board
TEENSY_15/A1/Buzzer: IC1.M12 (GPIO_AD_B1_03); also elsewhere on the board
TEENSY_16/A2: IC1.K10 (GPIO_AD_B1_07); also elsewhere on the board
TEENSY_17/A3: IC1.J12 (GPIO_AD_B1_06); also elsewhere on the board
TEENSY_18/A4/SDA/I2C_PIN: IC1.K11 (GPIO_AD_B1_01), R44.1; also elsewhere on the board
TEENSY_19/A5/SCL/I2C_PIN: IC1.J11 (GPIO_AD_B1_00), R43.1; also elsewhere on the board
TEENSY_20/A6: IC1.L13 (GPIO_AD_B1_10); also elsewhere on the board
TEENSY_24/A10: IC1.K14 (GPIO_AD_B0_12); also elsewhere on the board
TEENSY_25/A11: IC1.L14 (GPIO_AD_B0_13); also elsewhere on the board
TEENSY_28/PWM7: IC1.D5 (GPIO_EMC_32); also elsewhere on the board
TEENSY_29/PWM8: IC1.C5 (GPIO_EMC_31); also elsewhere on the board
TEENSY_30/DPIN1: IC1.E4 (GPIO_EMC_37); also elsewhere on the board
TEENSY_31/DPIN2: IC1.C3 (GPIO_EMC_36); also elsewhere on the board
TEENSY_32/DPIN3: IC1.C10 (GPIO_B0_12); also elsewhere on the board
TEENSY_33/PWM9: IC1.H4 (GPIO_EMC_07); also elsewhere on the board
Teensy_D+: IC1.L8 (USB_OTG1_DP); also elsewhere on the board
Teensy_D-: IC1.M8 (USB_OTG1_DN); also elsewhere on the board
W25Q_VDD_LED: C31.1, C36.1, C40.1, C45.1, D12.2, IC1.E6 (NVCC_EMC_1), IC1.E9 (NVCC_GPIO_1), IC1.F5 (NVCC_EMC_2), IC1.F10 (NVCC_GPIO_2), IC1.J6 (NVCC_SD0), IC1.J10 (NVCC_GPIO_3), IC1.K4 (DCDC__IN_Q), IC1.K5 (NVCC_SD1), IC1.N14 (VDDA_ADC_3P3), IC1.P12 (VDD_HIGH_IN), J31.4 (VDD), L3.2, R40.2, R43.2, R44.2, U15.5 (OUT); also elsewhere on the board

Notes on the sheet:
Primary MCU ( Teensy 4.1 )

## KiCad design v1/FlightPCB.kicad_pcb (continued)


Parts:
BZ1: Buzzer; Buzzer_CUI_CPT-9019S-SMT
D2: Teensy Power ( Yellow ); LED_0402_1005Metric
D3: 3.3V Power ( Green ); LED_0402_1005Metric
D4: RPI2040 Status ( Orange ); LED_0402_1005Metric
D5: Pyro Arm ( Red ); LED_0402_1005Metric
D6: Teensy 13 ( Orange ); LED_0402_1005Metric
D7: RPI2040 Power ( Yellow ); LED_0402_1005Metric
D8: GPS ( Blue ); LED_0402_1005Metric
D9: Teensy Status; IN-PI22TAT5R5G5B
D10: RPI2040 Status; IN-PI22TAT5R5G5B
D13: Xbee ( Orange ); LED_0402_1005Metric
H1, H2, H3, H4: MountingHole_Pad; MountingHole_2.7mm_M2.5_Pad_Via
R15, R17, R18, R19, R20, R21, R22, R23, R24, R32: 1k; R_0603_1608Metric
R27: DNF; R_0603_1608Metric

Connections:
+3.3V: D3.2 (A); also elsewhere on the board
+5V: D9.3 (A2), D10.3 (A2); also elsewhere on the board
BARO_SCK/Teensy: D6.2 (A); also elsewhere on the board
BatteryTerminal-: D9.1 (A1), D10.1 (A1), H1.1, H2.1, H3.1, H4.1, R17.2, R18.2, R19.2, R20.2, R21.2, R23.2, R27.2, R32.2; also elsewhere on the board
GPS_TIMEPULSE: D8.2 (A); also elsewhere on the board
MKL_PTB3_LED: R15.2; also elsewhere on the board
unnamed: BZ1.2 (-), R27.1
unnamed: D2.1 (K), R15.1
unnamed: D3.1 (K), R17.1
unnamed: D4.1 (K), R18.1
unnamed: D5.1 (K), R19.1
unnamed: D6.1 (K), R20.1
unnamed: D7.1 (K), R21.1
unnamed: D8.1 (K), R23.1
unnamed: D9.2 (K1), R22.2
unnamed: D10.2 (K1), R24.2
unnamed: D13.1 (K), R32.1
PYRO_ARM+: D5.2 (A); also elsewhere on the board
RPI2040_GPIO13/Status LED: R24.1; also elsewhere on the board
RPI2040_GPIO25_STATUS: D4.2 (A); also elsewhere on the board
RPI2040_POWER: D7.2 (A); also elsewhere on the board
SX12_CONN_STATUS: D13.2 (A); also elsewhere on the board
TEENSY_15/A1/Buzzer: BZ1.1 (+); also elsewhere on the board
TEENSY_20/A6: R22.1; also elsewhere on the board
W25Q_VDD_LED: D2.2 (A); also elsewhere on the board


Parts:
C27, C34, C35, C44, C48: 0.22uF; C_0402_1005Metric
C32, C39: 4.7uF; C_0603_1608Metric
C50, C51: 12pF; C_0402_1005Metric
C52, C53: 20pF; C_0402_1005Metric
IC1: MIMXRT1062DVJ6B; BGA196C80P14X14_1200X1200X152; Mouser Part Number 771-MIMXRT1062DVJ6B
R41: 100k; R_0603_1608Metric
R42: 2.2M; R_0603_1608Metric
TP11: PTB2; TestPoint_Pad_D1.0mm
TP15: VDD_SNVS; TestPoint_Pad_D1.0mm
U13: MKL02Z32VFG4; QFN-16-1EP_3x3mm_P0.5mm_EP1.9x1.9mm
U16, U17: W25Q64JVXGIM; XSON8_4x4mm
Y2: Crystal_GND23 24 MHz; Crystal_SMD_Abracon_ABM3B-4Pin_5.0x3.2mm
Y3: 32.768 kHz; Crystal_SMD_2012-2Pin_2.0x1.2mm

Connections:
BatteryTerminal-: C27.2, C32.2, C34.2, C35.2, C39.2, C44.2, C48.2, C50.2, C51.2, C52.2, C53.2, IC1.A1 (VSS_1), IC1.A14 (VSS_2), IC1.B5 (VSS_3), IC1.B10 (VSS_4), IC1.E2 (VSS_5), IC1.E13 (VSS_6), IC1.G7 (VSS_7), IC1.G8 (VSS_8), IC1.G14 (GPIO_AD_B0_05), IC1.H7 (VSS_9), IC1.H8 (VSS_10), IC1.J7 (VSS_11), IC1.J8 (VSS_12), IC1.K2 (VSS_13), IC1.K9 (NGND_KEL0), IC1.K13 (VSS_14), IC1.L9 (VSS_15), IC1.N1 (DCDC_GND_1), IC1.N2 (DCDC_GND_2), IC1.N5 (VSS_16), IC1.N8 (VSS_17), IC1.P1 (VSS_18), IC1.P14 (VSS_19), R41.2, R42.2, U13.2 (VSS/VREFL), U13.17 (EPAD), U16.4 (GND), U17.4 (GND), Y2.2, Y2.4; also elsewhere on the board
MKL_PTB3_LED: U13.11 (PTB3/IRQ_10); also elsewhere on the board
unnamed: IC1.G10 (GPIO_AD_B0_11), IC1.K3 (DCDC_PSWITCH), R41.1, U13.3 (PTA3)
unnamed: IC1.F11 (GPIO_AD_B0_04), U13.4 (PTA4)
unnamed: IC1.E14 (GPIO_AD_B0_06), U13.5 (PTA5)
unnamed: IC1.F12 (GPIO_AD_B0_07), U13.8 (PTB0/IRQ_5)
unnamed: IC1.F13 (GPIO_AD_B0_08), U13.13 (PTB5/IRQ_12)
unnamed: IC1.F14 (GPIO_AD_B0_09), U13.7 (PTA7/IRQ_4)
unnamed: IC1.G13 (GPIO_AD_B0_10), U13.6 (PTA6)
unnamed: IC1.D10 (GPIO_B0_13), U13.12 (PTB4/IRQ_11)
unnamed: IC1.F3 (GPIO_EMC_01), U13.15 (PTA1/IRQ_1/LPTMR0_ALT1)
unnamed: IC1.F1 (GPIO_EMC_22), U16.1 (CS)
unnamed: IC1.D2 (GPIO_EMC_25), U16.6 (CLK)
unnamed: IC1.B3 (GPIO_EMC_26), U16.5 (D0)
unnamed: IC1.A2 (GPIO_EMC_27), U16.2 (D1)
unnamed: IC1.D1 (GPIO_EMC_28), U16.3 (D2)
unnamed: IC1.E1 (GPIO_EMC_29), U16.7 (D3)
unnamed: IC1.L3 (GPIO_SD_B1_06), U17.1 (CS)
unnamed: IC1.L4 (GPIO_SD_B1_07), U17.6 (CLK)
unnamed: IC1.P3 (GPIO_SD_B1_08), U17.5 (D0)
unnamed: IC1.N4 (GPIO_SD_B1_09), U17.2 (D1)
unnamed: IC1.P4 (GPIO_SD_B1_10), U17.3 (D2)
unnamed: IC1.P5 (GPIO_SD_B1_11), U17.7 (D3)
unnamed: C39.1, C44.1, IC1.P10 (NVCC_PLL)
unnamed: IC1.M7 (POR_B), U13.9 (PTB1/IRQ_6)
unnamed: C53.1, IC1.N9 (RTC_XTALI), Y3.2
unnamed: C52.1, IC1.P9 (RTC_XTALO), Y3.1
unnamed: C32.1, C35.1, IC1.P8 (VDD_HIGH_CAP)
unnamed: C48.1, IC1.M10 (VDD_SNVS_CAP), TP15.1
unnamed: C51.1, IC1.P11 (XTALI), R42.1, Y2.1
unnamed: C50.1, IC1.N11 (XTALO), Y2.3
unnamed: TP11.1, U13.10 (PTB2/IRQ_7)
W25Q_VDD_LED: C27.1, C34.1, U13.1 (VDD/VREFH), U16.8 (VDD), U17.8 (VDD); also elsewhere on the board

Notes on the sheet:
Primary MCU ( Teensy 4.1 )


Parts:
F1, F2: Polyfuse; Fuse_1206_3216Metric
F3: Polyfuse; Fuse_1812_4532Metric
J1: Teensy USB_C_Receptacle; GCT_USB4105-GF-A; PARTREV B3
J2: Power In; TerminalBlock_Phoenix_PT-1,5-2-5.0-H_1x02_P5.00mm_Horizontal
J3: Enable Power; TerminalBlock_Phoenix_PT-1,5-2-5.0-H_1x02_P5.00mm_Horizontal
J4: Pyro Arm; TerminalBlock_Phoenix_PT-1,5-2-5.0-H_1x02_P5.00mm_Horizontal
J5: Pyro 1; TerminalBlock_Phoenix_PT-1,5-2-5.0-H_1x02_P5.00mm_Horizontal
J6: Pyro 2; TerminalBlock_Phoenix_PT-1,5-2-5.0-H_1x02_P5.00mm_Horizontal
J7: Pyro 3; TerminalBlock_Phoenix_PT-1,5-2-5.0-H_1x02_P5.00mm_Horizontal
J10: Pyro 4; TerminalBlock_Phoenix_PT-1,5-2-5.0-H_1x02_P5.00mm_Horizontal
J11: PinHeader_3x05_P2.54mm_Vertical_Left
J12: Teensy Pins; PinSocket_2x09_P2.54mm_Vertical
J13: RPI2040 Pins; PinSocket_2x09_P2.54mm_Vertical
J14: PinHeader_3x05_P2.54mm_Vertical_Right
J15: RPI2040 USB_C_Receptacle; GCT_USB4105-GF-A; PARTREV B3
Q2, Q3, Q4, Q5: ZXMN2F30FH; SOT-23
R1, R2, R14, R16: 5.1k; R_0603_1608Metric
R3, R4, R7, R37: 1; R_0603_1608Metric
R9, R11, R12, R38: 470; R_0603_1608Metric
R39, R55, R57, R59: 100k; R_0603_1608Metric
R53, R54, R56, R58: 27k; R_0603_1608Metric

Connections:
+3.3V: J12.13, J13.14; also elsewhere on the board
+5V: F1.1, F2.2, J11.8 (5V), J11.9 (5V), J11.10 (5V), J11.11 (5V), J11.12 (5V), J11.13 (5V), J11.14 (5V), J14.8 (5V), J14.9 (5V), J14.10 (5V), J14.11 (5V), J14.12 (5V), J14.13 (5V), J14.14 (5V); also elsewhere on the board
BARO_MISO/Teensy: J12.6; also elsewhere on the board
BARO_MOSI/Teensy: J12.8; also elsewhere on the board
BARO_SCK/Teensy: J12.12; also elsewhere on the board
BatteryTerminal+: F3.2, J3.2; also elsewhere on the board
BatteryTerminal-: J1.A1_B12 (GND), J1.B1_A12 (GND__1), J1.SH1 (SHELL_GND), J1.SH2 (SHELL_GND__1), J1.SH3 (SHELL_GND__2), J1.SH4 (SHELL_GND__3), J2.1, J11.1 (GND), J11.2 (GND), J11.3 (GND), J11.4 (GND), J11.5 (GND), J11.6 (GND), J11.7 (GND), J12.15, J13.16, J14.1 (GND), J14.2 (GND), J14.3 (GND), J14.4 (GND), J14.5 (GND), J14.6 (GND), J14.7 (GND), J15.A1_B12 (GND), J15.B1_A12 (GND__1), J15.SH1 (SHELL_GND), J15.SH2 (SHELL_GND__1), J15.SH3 (SHELL_GND__2), J15.SH4 (SHELL_GND__3), Q2.2 (S), Q3.2 (S), Q4.2 (S), Q5.2 (S), R1.1, R2.1, R9.2, R11.2, R12.2, R14.1, R16.1, R38.2, R53.1, R54.1, R56.1, R58.1; also elsewhere on the board
unnamed: J1.A5 (CC1), R2.2
unnamed: J1.B5 (CC2), R1.2
unnamed: J2.2, J3.1
unnamed: F3.1, J4.1
unnamed: J5.2, R7.2
unnamed: J6.2, R3.2
unnamed: J7.2, R4.2
unnamed: J10.2, R37.2
unnamed: F1.2, J12.17
unnamed: F2.1, J13.18
unnamed: J15.A5 (CC1), R16.2
unnamed: J15.B5 (CC2), R14.2
unnamed: Q2.3 (D), R3.1, R39.2
unnamed: Q3.3 (D), R4.1, R57.2
unnamed: Q4.3 (D), R37.1, R59.2
unnamed: Q5.3 (D), R7.1, R55.2
PYRO1_SENSE: R54.2, R55.1; also elsewhere on the board
PYRO1_TRIGGER/Teensy_21/A7: Q5.1 (G), R12.1; also elsewhere on the board
PYRO2_SENSE: R39.1, R53.2; also elsewhere on the board
PYRO2_TRIGGER/Teensy_22/A8: Q2.1 (G), R9.1; also elsewhere on the board
PYRO3_SENSE: R56.2, R57.1; also elsewhere on the board
PYRO3_TRIGGER/Teensy_23/A9: Q3.1 (G), R11.1; also elsewhere on the board
PYRO4_SENSE: R58.2, R59.1; also elsewhere on the board
PYRO4_TRIGGER/Teensy_41/A17: Q4.1 (G), R38.1; also elsewhere on the board
PYRO_ARM+: J4.2, J5.1, J6.1, J7.1, J10.1; also elsewhere on the board
RPI2040_D0/TX/Serial_Pin: J13.1; also elsewhere on the board
RPI2040_D1/RX/Serial_Pin: J13.3; also elsewhere on the board
RPI2040_D+: J15.A6 (DP1), J15.B6 (DP2); also elsewhere on the board
RPI2040_D-: J15.A7 (DN1), J15.B7 (DN2); also elsewhere on the board
RPI2040_GPIO2/I2C1_SDA/I2C_PIN: J13.13; also elsewhere on the board
RPI2040_GPIO3/I2C1_SCL/I2C_PIN: J13.15; also elsewhere on the board
RPI2040_GPIO6/DPIN1: J13.2; also elsewhere on the board
RPI2040_GPIO7/DPIN2: J13.4; also elsewhere on the board
RPI2040_GPIO8/PWM11: J14.16 (SIG); also elsewhere on the board
RPI2040_GPIO9/PWM12: J14.15 (SIG); also elsewhere on the board
RPI2040_GPIO10/DPIN5: J13.17; also elsewhere on the board
RPI2040_GPIO12/PWM10: J14.17 (SIG); also elsewhere on the board
RPI2040_GPIO14/SS/SPI_PIN: J13.9; also elsewhere on the board
RPI2040_GPIO16/MISO/SPI_PIN: J13.5; also elsewhere on the board
RPI2040_GPIO18/SCK/SPI_PIN: J13.11; also elsewhere on the board
RPI2040_GPIO19/MOSI/SPI_PIN: J13.7; also elsewhere on the board
RPI2040_GPIO21/DPIN6: J13.6; also elsewhere on the board
RPI2040_GPIO22/DPIN7: J13.8; also elsewhere on the board
RPI2040_GPIO26/A0/APIN1: J13.10; also elsewhere on the board
RPI2040_GPIO27/A1/APIN2: J13.12; also elsewhere on the board
TEENSY_0/RX1: J11.21 (SIG); also elsewhere on the board
TEENSY_1/TX1: J11.20 (SIG); also elsewhere on the board
TEENSY_2/PWM1: J14.18 (SIG); also elsewhere on the board
TEENSY_3/PWM2: J11.18 (SIG); also elsewhere on the board
TEENSY_4/PWM3: J11.17 (SIG); also elsewhere on the board
TEENSY_5/PWM4: J11.16 (SIG); also elsewhere on the board
TEENSY_6/PWM5: J11.15 (SIG); also elsewhere on the board
TEENSY_7/RX2/Serial_Pin: J12.4; also elsewhere on the board
TEENSY_8/TX2/Serial_Pin: J12.2; also elsewhere on the board
TEENSY_10/CS/SPI_PIN: J12.10; also elsewhere on the board
TEENSY_14/A0/PWM6: J11.19 (SIG); also elsewhere on the board
TEENSY_16/A2: J12.18; also elsewhere on the board
TEENSY_17/A3: J12.7; also elsewhere on the board
TEENSY_18/A4/SDA/I2C_PIN: J12.14; also elsewhere on the board
TEENSY_19/A5/SCL/I2C_PIN: J12.16; also elsewhere on the board
TEENSY_24/A10: J12.9; also elsewhere on the board
TEENSY_25/A11: J12.11; also elsewhere on the board
TEENSY_28/PWM7: J14.20 (SIG); also elsewhere on the board
TEENSY_29/PWM8: J14.19 (SIG); also elsewhere on the board
TEENSY_30/DPIN1: J12.1; also elsewhere on the board
TEENSY_31/DPIN2: J12.3; also elsewhere on the board
TEENSY_32/DPIN3: J12.5; also elsewhere on the board
TEENSY_33/PWM9: J14.21 (SIG); also elsewhere on the board
Teensy_D+: J1.A6 (DP1), J1.B6 (DP2); also elsewhere on the board
Teensy_D-: J1.A7 (DN1), J1.B7 (DN2); also elsewhere on the board

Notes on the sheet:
need esd protection, usblc6-2scc6
Input 6V - 26V


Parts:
C54, C64: 1uF; C_0603_1608Metric
C55, C56, C57, C58, C59, C60, C61, C62, C63, C65: 100nF; C_0603_1608Metric
C66, C67: 27pF; C_0603_1608Metric
C68: 10uF; C_0603_1608Metric
R36: DNF; R_0603_1608Metric
R45, R46: 1k; R_0603_1608Metric
R47, R48, R51, R52: 2.2k; R_0603_1608Metric
R49, R50: 27; R_0603_1608Metric
TP25: SWCLK; TestPoint_Pad_D1.0mm
TP26: SWD; TestPoint_Pad_D1.0mm
TP27: Run; TestPoint_Pad_D1.0mm
TP28: RPI2040_GPIO11; TestPoint_Pad_D1.0mm
U19: RP2040; RP2040-QFN-56
U20: W25Q128JVSIQ; SOIC-8_5.23x5.23mm_P1.27mm
Y4: Crystal; Crystal_SMD_Abracon_ABM8G-4Pin_3.2x2.5mm

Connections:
+3.3V: C54.1, C55.1, C56.1, C57.1, C58.1, C59.1, C60.1, C61.1, C65.1, C68.1, R36.1, R47.1, R48.1, R51.1, R52.1, U19.1 (IOVDD), U19.10 (IOVDD), U19.22 (IOVDD), U19.33 (IOVDD), U19.42 (IOVDD), U19.43 (ADC_AVDD), U19.44 (VREG_IN), U19.48 (USB_VDD), U19.49 (IOVDD), U20.8 (VCC); also elsewhere on the board
BARO_MISO/Teensy: U19.36 (GPIO24); also elsewhere on the board
BARO_MOSI/Teensy: U19.39 (GPIO27_ADC1); also elsewhere on the board
BARO_SCK/Teensy: U19.38 (GPIO26_ADC0); also elsewhere on the board
BatteryTerminal-: C54.2, C55.2, C56.2, C57.2, C58.2, C59.2, C60.2, C61.2, C62.2, C63.2, C64.2, C65.2, C66.1, C67.2, C68.2, U19.19 (TESTEN), U19.57 (GND), U20.4 (GND); also elsewhere on the board
EXTINT GPS/RPI2040: U19.28 (GPIO17); also elsewhere on the board
INA_SCL_RPI2040: R48.2, U19.7 (GPIO5); also elsewhere on the board
INA_SDA_RPI2040: R47.2, U19.6 (GPIO4); also elsewhere on the board
unnamed: C67.1, R46.2, Y4.1
unnamed: TP28.1, U19.14 (GPIO11)
unnamed: U19.52 (QSPI_SCLK), U20.6 (CLK)
unnamed: U19.53 (QSPI_SD0), U20.5 (DI(IO0))
unnamed: U19.55 (QSPI_SD1), U20.2 (DO(IO1))
unnamed: U19.54 (QSPI_SD2), U20.3 (IO2)
unnamed: U19.51 (QSPI_SD3), U20.7 (IO3)
unnamed: R36.2, R45.2, U19.56 (QSPI_SS), U20.1 (~CS)
unnamed: TP27.1, U19.26 (RUN)
unnamed: TP25.1, U19.24 (SWCLK)
unnamed: TP26.1, U19.25 (SWD)
unnamed: R50.2, U19.46 (USB_DM)
unnamed: R49.2, U19.47 (USB_DP)
unnamed: C66.2, U19.20 (XIN), Y4.2
unnamed: R46.1, U19.21 (XOUT)
RPI2040_D0/TX/Serial_Pin: U19.2 (GPIO0); also elsewhere on the board
RPI2040_D1/RX/Serial_Pin: U19.3 (GPIO1); also elsewhere on the board
RPI2040_D+: R49.1; also elsewhere on the board
RPI2040_D-: R50.1; also elsewhere on the board
RPI2040_GPIO2/I2C1_SDA/I2C_PIN: R51.2, U19.4 (GPIO2); also elsewhere on the board
RPI2040_GPIO3/I2C1_SCL/I2C_PIN: R52.2, U19.5 (GPIO3); also elsewhere on the board
RPI2040_GPIO6/DPIN1: U19.8 (GPIO6); also elsewhere on the board
RPI2040_GPIO7/DPIN2: U19.9 (GPIO7); also elsewhere on the board
RPI2040_GPIO8/PWM11: U19.11 (GPIO8); also elsewhere on the board
RPI2040_GPIO9/PWM12: U19.12 (GPIO9); also elsewhere on the board
RPI2040_GPIO10/DPIN5: U19.13 (GPIO10); also elsewhere on the board
RPI2040_GPIO12/PWM10: U19.15 (GPIO12); also elsewhere on the board
RPI2040_GPIO13/Status LED: U19.16 (GPIO13); also elsewhere on the board
RPI2040_GPIO14/SS/SPI_PIN: U19.17 (GPIO14); also elsewhere on the board
RPI2040_GPIO16/MISO/SPI_PIN: U19.27 (GPIO16); also elsewhere on the board
RPI2040_GPIO18/SCK/SPI_PIN: U19.29 (GPIO18); also elsewhere on the board
RPI2040_GPIO19/MOSI/SPI_PIN: U19.30 (GPIO19); also elsewhere on the board
RPI2040_GPIO21/DPIN6: U19.32 (GPIO21); also elsewhere on the board
RPI2040_GPIO22/DPIN7: U19.34 (GPIO22); also elsewhere on the board
RPI2040_GPIO25_STATUS: U19.37 (GPIO25); also elsewhere on the board
RPI2040_GPIO26/A0/APIN1: U19.40 (GPIO28_ADC2); also elsewhere on the board
RPI2040_GPIO27/A1/APIN2: U19.41 (GPIO29_ADC3); also elsewhere on the board
RPI2040_POWER: C62.1, C63.1, C64.1, U19.23 (DVDD), U19.45 (VREG_VOUT), U19.50 (DVDD); also elsewhere on the board
SX12_CS/RPI2040: U19.18 (GPIO15); also elsewhere on the board
TEENSY_9/RPI2040_GPIO20_CS: U19.31 (GPIO20); also elsewhere on the board

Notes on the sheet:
mybe YSX321SL
PWM limits https://forums.raspberrypi.com/viewtopic.php?t=316931
secondary spi pins
put these 27ohm resistor close to rpi2040
Make sure C54 ( 1uF ) is close to pin 44 of RP2040
Secondary MCU ( RP2040 )
Make sure C64 ( 1uF ) is close to pin 45 of RP2040



Board: 4 copper layers, 49.6 x 99.8 mm, 204 parts (168 on the bottom side), 198 nets.
